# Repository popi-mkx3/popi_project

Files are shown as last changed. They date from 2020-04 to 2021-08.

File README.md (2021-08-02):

# POPI


<br>
<br>

## News : Walko
Below are the links to the follow up of the POPI project, on a new quadruped. Our whole work will be once again open source and we should start releasing it in September 2021. <br>
The goal is still the same : allowing everybody to build their own quad. Unlike POPI, our new quad will be 100% 3d-printed to make this goal closer, with components available to purchase online. We will provide as soon as possible a BOM and links to the manufacturers' websites (we are not resellers). <br>
According to our current estimations, building your own quad will cost around 2,7k€ altogether (without the camera module though), which is still expensive but rather cheap when considering the size of the robot and the price of similar-sized robots.
<br>
We aim to provide beginner-friendly step-by-step instructions along the road, and to keep improving the tech as well.
<br>
<br>
If you want to stay tuned about this : <br>
[Website](https://walko-robotics.com) <br>
[GitLab](https://gitlab.com/walko-robotics/doge/software) and [GitHub](https://github.com/Walko-Robotics) - Please keep in mind that the GitHub repo will be a mirror of the GitLab one from now on. <br>
[Instagram](https://www.instagram.com/walko_adventures/) <br>
[Discord](dsc.gg/walko) <br>
[YouTube](https://www.youtube.com/c/WalkoRobotics) <br> <br>
Fair warning : we mainly use French on our social media for now, but you can still DM us or send us an email at contact.walko@gmail.com if you want.
<br> <br>

## Overview of the project
POPI is an entirely open-source quadruped robot. Though not yet extremely agile, <a href="#team">we</a> meant it to be accessible to anyone interested in robotics and we hope it becomes a friendly collaborative platform for educational or research purposes. You will hence find in this repository everything there is to know about POPI. If you want to know about every details, a good way would be to have a look at the user manual in the [popi_reports] folder.

This project initially started as a student work. As a team of 10 not-yet engineers, we designed and built it from scratch with a 4k€ budget over a six-month-long period during which we still had to take other classes and exams. As such, we are proud of what we achieved but we do know POPI couldn't compete with other quadrupeds as-is. Some of us are still working on this prototype on our free time to improve it, and we will share here everything. In the same time we are also rethinking the whole design to create a new, lighter and mostly 3D-printed POPI.

We are actually looking for some fundings to get this new version up and running and are interested in any opportunity we could have to continue our work. If you have any idea about this or would like to discuss some kind of partnership, please let us know by sending us an <a href = "mailto: popi.mkx3@gmail.com">email</a>.

Otherwise, you can still have a look at what we've done so far on this first prototype. Please keep in mind we inevitably made some mistakes considering it is our first robot and we had limited time and budget. We'll be more than happy to get some advice and discuss any part of our work with you.

#### What is available
:heavy_check_mark: User manual  
:heavy_check_mark: Bill of materials  
:heavy_check_mark: Mechanical drawings and CAD files  
:heavy_check_mark: Electrical drawings  
:heavy_check_mark: Source code (ROS and C++)  
:heavy_check_mark: Cool 3D-renders and wallpapers  
<br>
<br>

<p align="center">
  <a href="#build">Build your own POPI</a> •
  <a href="#contribute">Contribute</a> •
  <a href="#alternative">Other open-source quadrupeds</a> •
  <a href="#team">Meet the team</a> •
  <a href="#acknowledgments">Acknowledgments</a>
</p>

<p align="center">
<a target="_blank" rel="noopener noreferrer" href="https://www.youtube.com/watch?v=yvZBiybOPDk" title="Watch the teaser on YouTube">Watch the teaser on YouTube</a>
</p>

##  Build your own POPI
We really hope you build your own POPI, and if that's the case and you ever need our help, we'll be happy to answer all your questions. To get you going you will find all the CAD files and mechanical drawings in the [popi_mechanics] folder, along with information about POPI's dimensions, its actuators' specifications and the machines we used to make its parts.

In [popi_electronics] you will learn more about POPI's electrical needs, its wiring maps and the electronic supplies. You can also check the whole bill of materials [here](https://github.com/popi-mkx3/popi_project/blob/master/popi_reports/POPI_bill_of_materials.xlsx).

The source code is entirely based on [ROS]. <b>Even if you don't plan on building POPI, you can still develop your own code or your own walking trajectories and try it on a virtual POPI !</b> The instructions to download the source code and use it are available in the [popi_software] folder. Of course you will also find there more explanations about how it works to help you getting started.
<br>
<br>

## Contribute
In times when [ICRA] organizes workshops called *["Towards real-world deployment of legged robots"](https://www.youtube.com/watch?v=nKZdYw9eXY0)*, and when big shots like MIT and Boston Dynamics [loan](http://news.mit.edu/2019/mit-mini-cheetah-first-four-legged-robot-to-backflip-0304) or [sell](https://spectrum.ieee.org/automaton/robotics/industrial-robots/boston-dynamics-spot-robot-dog-goes-on-sale) their robots, we hope our modest open-source alternative can contribute to spread this technology.

The whole point of making this project fully open-source is to have anyone who is interested contribute to POPI ! Whether it includes documentation translations, new functionalities, bug fixes or code improvements, we'll be glad to receive your pull request.

We're fully aware we still have a long road to go before POPI becomes a more autonomous robot, and we'll be happy to take anyone with us onboard. You can see here the list of [contributors](https://github.com/popi-mkx3/popi_project/graphs/contributors) who participated in this project.
<br>
<br>

##  Other open-source quadrupeds
Other open-source quadruped robots already exist ! If you are interested, you can check out the [Stanford Doggo Project] or the [Open Dynamic Robot Initiative] which are really cool and more functional at this point in time.

If you know of other advanced open-source robots do not hesitate to contact us, we will be really happy to have a look at other projects.
<br>
<br>

##  Meet the team !
POPI was initially designed as part of our mechatronical engineering degree at IMT Mines d'Alès in France. Here is the team who started this project.
If you want to contact us you can send us an email at popi.mkx3@gmail.com.

<br>
<p align="center"><b> Project Leader </b></p>
<p align="center">
  <a target="_blank" rel="noopener noreferrer" href="https://www.linkedin.com/in/clément-thomaso-6b9ab910b/">Clément Thomaso</a>
</p>

<p align="center"><b> Mechanics </b> &nbsp; &nbsp; &nbsp; &nbsp; &nbsp; &nbsp; &nbsp; &nbsp; &nbsp; &nbsp; &nbsp; &nbsp; &nbsp; &nbsp; &nbsp; &nbsp; &nbsp; &nbsp; &nbsp; &nbsp; &nbsp; &nbsp; &nbsp; <b> Electronics </b> &nbsp; &nbsp; &nbsp; &nbsp; &nbsp; &nbsp; &nbsp; &nbsp; &nbsp; &nbsp; &nbsp; &nbsp; &nbsp; &nbsp; &nbsp; &nbsp; &nbsp; &nbsp; &nbsp; &nbsp; &nbsp; &nbsp; &nbsp; <b> Programming </b></p>

<p align="center">
  <a target="_blank" rel="noopener noreferrer" href="https://www.linkedin.com/in/rémi-combacal-16032214a/">Rémi Combacal</a>
  <a target="_blank" rel="noopener noreferrer" href="https://www.linkedin.com/in/anaïs-gutton-655383a6/">Anaïs Aharram-Gutton</a>
  <a target="_blank" rel="noopener noreferrer" href="https://www.linkedin.com/in/olivier-peres/">Olivier Peres</a>
  <a target="_blank" rel="noopener noreferrer" href="https://www.linkedin.com/in/guillaume-rougé-913a10108/">Guillaume Rougé</a>
  <a target="_blank" rel="noopener noreferrer" href="https://www.linkedin.com/in/clémence-graton-a02200174/">Clémence Graton</a>
  <a target="_blank" rel="noopener noreferrer" href="https://www.linkedin.com/in/jean-pelloux-prayer-b38a32143/">Jean Pelloux-Prayer</a>
  <a target="_blank" rel="noopener noreferrer" href="https://www.linkedin.com/in/yannis-oddon-442717128/">Yannis Oddon</a>
  <a target="_blank" rel="noopener noreferrer" href="https://www.linkedin.com/in/karla-brottet-69440/">Karla Brottet</a>
  <a target="_blank" rel="noopener noreferrer" href="https://www.linkedin.com/in/lucas-labarussiat/">Lucas Labarussiat</a>
</p>
<br>
<br>

## Acknowledgments
First we would like to thank deeply [Alexander W. Winkler] and [Dave Coleman] for their respective work on [Towr] and [ROS control boilerplate].  
Then let us thank [TiMOTION] who gave us some precious advice along with our knee actuators. Without their contribution, POPI wouldn't be able to lift his legs !  
Finally we of course want to express our sincere gratitude to all our teachers from [IMT Mines d'Alès] who gave us the opportunity to undertake this project and were there to lend us a hand when we needed it the most.
<br>
<br>

 &nbsp; &nbsp; &nbsp; &nbsp; &nbsp; &nbsp; &nbsp; &nbsp; &nbsp; &nbsp; &nbsp; &nbsp; &nbsp;  &nbsp; &nbsp; &nbsp; &nbsp; &nbsp; &nbsp; &nbsp; &nbsp; &nbsp; &nbsp; &nbsp; &nbsp; &nbsp; 

[popi_reports]: https://github.com/popi-mkx3/popi_project/tree/master/popi_reports
[popi_mechanics]: https://github.com/popi-mkx3/popi_project/tree/master/popi_mechanics
[popi_electronics]: https://github.com/popi-mkx3/popi_project/tree/master/popi_electronics
[popi_software]: https://github.com/popi-mkx3/popi_project/tree/master/popi_software

[ROS]: https://www.ros.org/
[Towr]: https://github.com/ethz-adrl/towr
[rqt_bag]: http://wiki.ros.org/rqt_bag
[xpp]: http://wiki.ros.org/xpp
[RViz]: http://wiki.ros.org/rviz
[URDF]: http://wiki.ros.org/urdf
[Gazebo]: http://gazebosim.org/
[rqt_gui]: http://wiki.ros.org/rqt_gui
[ROS Melodic]: http://wiki.ros.org/melodic/Installation/Ubuntu

[BalenaEtcher]: https://www.minimachines.net/tutos/etcher-flasher-image-usb-50144
[ROS control boilerplate]: https://github.com/PickNikRobotics/ros_control_boilerplate

[Alexander W. Winkler]: https://www.alex-winkler.com
[Dave Coleman]: http://dav.ee/
[TiMOTION]: https://www.timotion.com/fr
[IMT Mines d'Alès]: https://www.mines-ales.fr/
[ICRA]: https://www.icra2020.org/
[Stanford Doggo Project]: https://github.com/Nate711/StanfordDoggoProject/blob/master/README.md
[Open Dynamic Robot Initiative]: https://open-dynamic-robot-initiative.github.io/
[YouTube channel]: https://www.youtube.com/channel/UCaCy-1MX6SoqdtjZH4uU_TA

[Clément]: https://www.linkedin.com/in/clément-thomaso-6b9ab910b/
[Rémi]: https://www.linkedin.com/in/rémi-combacal-16032214a/
[Anaïs]: https://www.linkedin.com/in/anaïs-gutton-655383a6/
[Olivier]: https://www.linkedin.com/in/olivier-peres/
[Guillaume]: https://www.linkedin.com/in/guillaume-rougé-913a10108/
[Clémence]: https://www.linkedin.com/in/clémence-graton-a02200174/
[Jean]: https://www.linkedin.com/in/jean-pelloux-prayer-b38a32143/
[Yannis]: https://www.linkedin.com/in/yannis-oddon-442717128/
[Karla]: https://www.linkedin.com/in/karla-brottet-69440/
[Lucas]: https://www.linkedin.com/in/lucas-labarussiat/

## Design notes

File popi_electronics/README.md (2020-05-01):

# popi_electronics


<br>
<br>

You will find here everything you need to understand all the electronics necessary to make POPI walk. Hence, all the [wiring diagrams] and the [pin planning] of our onboard-computers are available in this folder. These files unfortunately are in French for now, but the diagrams should still speak to anyone. Let us know if you ever need a translation and we'll do our best ! To get an overview of POPI's electronic design, please read the following information.

#### What is available
:heavy_check_mark: Design made with [easyEDA]  
:heavy_check_mark: Creation of a custom [encoder]  
:heavy_check_mark: Creation of a custom [current sensor PCB]  
:heavy_check_mark: Mapping of all the card to respect the symmetry  
:heavy_check_mark: PCB manufacturing on a PCB milling machine
<br>
<br>

<p align="center">
  <a href="#general-description">General description</a> •
  <a href="#onboard-computers">Onboard computers</a> •
  <a href="#sensors">Sensors</a> •
  <a href="#power-supply">Power supply</a> •
  <a href="#lets-look-further">Let's look further</a> •
  <a href="#contribute">Contribute</a> •
  <a href="#team">Meet the team</a>
</p>

<p align="center">
	
</p>

##  General description
Most of the electronics of the robot is located on the main electronic board underneath the plexiglass carter. All the parts are spread and layered evenly to ease the accessibility and the maintenance. As you can see below, the main electronic board is divided in 3 areas : computing, commanding and supplying.  
<p align="center">
	
</p>

All the details of the parts is given in the [electronic nomenclature] and a link to a retailer can be found in the [bills of material] in the [popi_report] repository. 
<br>
<br>

##  Onboard computers
POPI is embedded with 3 onboard computers. The main one is a [Raspberry Pi 3B+] and is used to host the controllers and compute the set point of each joint. It communicates with two [BeagleBone Black] (BBB) computers, each one managing the sensors and actuators of two legs (right legs for one BBB and left legs for the other). 

<p align="center">
	 
</p>
<br>
<br>

##  Sensors
In order to know the position of each joint, POPI is embedded with two kind of sensors. The knee and hip rolling joints positions are measured by potentiometers. For the hip pitching joints, we designed a custom [encoder] and its control PCB whose plan is available in this folder. 
<p align="center">
	 
</p>

We also designed a [current sensor PCB] to be able to know the consumption of the motors. All the details of this part are given in here.  
<br>
<br>
 
##  Power supply
POPI is actually powered by two 24V power supplies that are located outside the robot on a [power supply board] we designed. Thus, POPI must be hooked up with an umbilicus cable that will provide the power. Details about this power supply board are given in the [user manual]. 
<p align="center">
	 
</p>

##  Let's look further
This design remains a proof of concept, designed and built in a few months by students relatively new to this field. We now have to improve what we've done and take into account the problems we encountered to achieve a truly functional V2.
  
#### Thoughts for a future version:
* Try looking for more power efficient motors to reduce the size of the ombilicus cable and even maybe to design an onboard battery. 
* Be more careful of ECM influence on the quality of the sensor signals. Try having all the high power beneath the main electronic board and isolate better the two zones. Think about shielding the important data cables. 
* Try having always absolute sensors or at least add limit switches to the system. 
* Unfortunately we had not enough analog input to receive all the current sensor data in the same time. Try adding a multiplexer or an ADC on the current sensor PCB. 
* We had to add 100nF capacitors just before the BeagleBone to filter the analog signal of our potentiometers. Try designing a proper integration board for those capacitors.
<br>
<br>

## Contribute
The whole point of making this project fully open-source is to have anyone who is interested contribute to POPI ! Whether it includes documentation translations, new functionalities, bug fixes or code improvements, we'll be glad to receive your pull request.

We're fully aware we still have a long road to go before POPI becomes a more autonomous robot, and we'll be happy to take anyone with us onboard. You can see here the list of [contributors](https://github.com/popi-mkx3/popi_project/graphs/contributors) who participated in this project.
<br>
<br>

##  Meet the team !
If you want to contact us you can send us an email at popi.mkx3@gmail.com.

<p align="center"><b> Project Leader </b></p>
<p align="center">
  <a target="_blank" rel="noopener noreferrer" href="https://www.linkedin.com/in/clément-thomaso-6b9ab910b/">Clément Thomaso</a>
</p>

<p align="center"><b> Mechanics </b> &nbsp; &nbsp; &nbsp; &nbsp; &nbsp; &nbsp; &nbsp; &nbsp; &nbsp; &nbsp; &nbsp; &nbsp; &nbsp; &nbsp; &nbsp; &nbsp; &nbsp; &nbsp; &nbsp; &nbsp; &nbsp; &nbsp; &nbsp; <b> Electronics </b> &nbsp; &nbsp; &nbsp; &nbsp; &nbsp; &nbsp; &nbsp; &nbsp; &nbsp; &nbsp; &nbsp; &nbsp; &nbsp; &nbsp; &nbsp; &nbsp; &nbsp; &nbsp; &nbsp; &nbsp; &nbsp; &nbsp; &nbsp; <b> Programming </b></p>

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

 &nbsp; &nbsp; &nbsp; &nbsp; &nbsp; &nbsp; &nbsp; &nbsp; &nbsp; &nbsp; &nbsp; &nbsp; &nbsp;  &nbsp; &nbsp; &nbsp; &nbsp; &nbsp; &nbsp; &nbsp; &nbsp; &nbsp; &nbsp; &nbsp; &nbsp; &nbsp; 

[wiring diagrams]: https://github.com/popi-mkx3/popi_project/blob/master/popi_electronics/POPI_PlanElec_General.pdf
[pin planning]: https://github.com/popi-mkx3/popi_project/blob/master/popi_electronics/POPI_PinPlanning.xlsx
[easyEDA]: https://easyeda.com/fr
[encoder]:https://github.com/popi-mkx3/popi_project/blob/master/popi_electronics/POPI_PlanElec_Carte_roue_codeuse.pdf
[current sensor PCB]: https://github.com/popi-mkx3/popi_project/blob/master/popi_electronics/POPI_PlanElec_Capteur_courant.pdf
[electronic nomenclature]: https://github.com/popi-mkx3/popi_project/blob/master/popi_electronics/Nomenclature.xlsx
[bills of material]: https://github.com/popi-mkx3/popi_project/blob/master/popi_reports/POPI_bill_of_materials.xlsx
[Raspberry Pi 3B+]: https://www.raspberrypi.org/products/raspberry-pi-3-model-b-plus/
[BeagleBone Black]: https://beagleboard.org/black
[power supply board]: https://github.com/popi-mkx3/popi_project/blob/master/popi_electronics/Schematic_POPI-Platine-dalimentation_Sheet_1.pdf
[user manual]: https://github.com/popi-mkx3/popi_project/blob/master/popi_reports/POPI_user_manual.pdf
[popi_reports]: https://github.com/popi-mkx3/popi_project/tree/master/popi_reports

[Clément]: https://www.linkedin.com/in/clément-thomaso-6b9ab910b/
[Rémi]: https://www.linkedin.com/in/rémi-combacal-16032214a/
[Anaïs]: https://www.linkedin.com/in/anaïs-gutton-655383a6/
[Olivier]: https://www.linkedin.com/in/olivier-peres/
[Guillaume]: https://www.linkedin.com/in/guillaume-rougé-913a10108/
[Clémence]: https://www.linkedin.com/in/clémence-graton-a02200174/
[Jean]: https://www.linkedin.com/in/jean-pelloux-prayer-b38a32143/
[Yannis]: https://www.linkedin.com/in/yannis-oddon-442717128/
[Karla]: https://www.linkedin.com/in/karla-brottet-69440/
[Lucas]: https://www.linkedin.com/in/lucas-labarussiat/

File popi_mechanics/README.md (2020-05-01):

# popi_mechanics


<br>
<br>

You will find here everything you need for the [machining] and the [assembly] as well as the [mechanical drawings] of this 71kg and 1 meter long robot. These files unfortunately are in French for now, but the drawings should still speak to anyone. Let us know if you ever need a translation and we'll do our best ! To get an overview of POPI's mechanical design, please read the following information.

#### What is available
:heavy_check_mark: Design made with [CATIA]  
:heavy_check_mark: First estimates of forces and torques on [SimDesigner]  
:heavy_check_mark: Mechanical simulation and actuator's choice on [SolidWorks] Motion and [SolidWorks] Simulation  
:heavy_check_mark: Machining with CNC milling and turning machines, water jet cutting and 3D printing  
:heavy_check_mark: Rendering with [SolidWorks] Motion and [SolidWorks] PhotoView 360  
<br>
<br>

<p align="center">
  <a href="#general-description">General description</a> •
  <a href="#how-it-works">How it works</a> •
  <a href="#lets-look-further">Let's look further</a> •
  <a href="#contribute">Contribute</a> •
  <a href="#team">Meet the team</a>
</p>

<p align="center">
<a target="_blank" rel="noopener noreferrer" href="https://www.youtube.com/watch?v=yvZBiybOPDk" title="Watch the teaser on YouTube">Watch the teaser on YouTube</a>
</p>

##  General description
When standing in its nominal position, POPI has the following general dimensions: 1017mm x 662mm x 620mm (DxLxH). The general assembly is available in the [CATIA folder]. You can download the whole folder and open the top assembly "ALL10-FinalVersion.CATProduct" with CATIA V5.
<p align="center">
	
</p>

As shown below, some accessories are needed for the proper handling of the robot, such as a base and handles. Their CAD is available as well in the [CATIA folder] with the respective names ["Socle"] and ["Poignee"].

<p align="center">
	 
</p>
<br>
<br>

##  How it works
POPI has a longitudinal axis of symmetry.

<p align="center">
	 
</p>
<br>
<br>
POPI is composed of 12 actuators, 3 per leg. The combination of the "pitching hip joint" and "knee joint" actuators allows the robot to operate linearly. The action of the "rolling hip joint" allows the robot to turn and keep balance. You can find details about the actuators [here].

<p align="center">
	 
</p>
<br>
<br>
Zoom on a leg and its actuators without the body:
<p align="center">
	 
</p>
<br>
<br>

##  Let's look further
This design remains a proof of concept, designed and built in a few months by students relatively new to this field. We now have to improve what we've done and take into account the problems we encountered to achieve a truly functional V2.
  
#### Thoughts for a future version:
* Do not make legs too heavy compared to the body and think ahead about the robot's balance. We currently have too much weight on the back compared to the front, so the rear feet are struggling to get off the ground.
* Think about the programming in parallel of mechanics, try out all possible approaches in a physical simulation of walking before machining the robot. SolidWorks Motion does this perfectly. 
* Our robot can move all of its joints independently, it's cool, but think about whether this is really useful. Moving the robot's pitch hip proportionally to the knee might be enough.
* Our robot is built in a simple way, that's the goal, but a slightly more complex arrangement that would allow the knee to move without a cylinder could be more efficient. A motor, which could be integrated into the body and act on the knee through a chain/pulley system might be a better solution.
<br>
<br>

## Contribute
The whole point of making this project fully open-source is to have anyone who is interested contribute to POPI ! Whether it includes documentation translations, new functionalities, bug fixes or code improvements, we'll be glad to receive your pull request.

We're fully aware we still have a long road to go before POPI becomes a more autonomous robot, and we'll be happy to take anyone with us onboard. You can see here the list of [contributors](https://github.com/popi-mkx3/popi_project/graphs/contributors) who participated in this project.
<br>
<br>

##  Meet the team !
If you want to contact us you can send us an email at popi.mkx3@gmail.com.

<p align="center"><b> Project Leader </b></p>
<p align="center">
  <a target="_blank" rel="noopener noreferrer" href="https://www.linkedin.com/in/clément-thomaso-6b9ab910b/">Clément Thomaso</a>
</p>

<p align="center"><b> Mechanics </b> &nbsp; &nbsp; &nbsp; &nbsp; &nbsp; &nbsp; &nbsp; &nbsp; &nbsp; &nbsp; &nbsp; &nbsp; &nbsp; &nbsp; &nbsp; &nbsp; &nbsp; &nbsp; &nbsp; &nbsp; &nbsp; &nbsp; &nbsp; <b> Electronics </b> &nbsp; &nbsp; &nbsp; &nbsp; &nbsp; &nbsp; &nbsp; &nbsp; &nbsp; &nbsp; &nbsp; &nbsp; &nbsp; &nbsp; &nbsp; &nbsp; &nbsp; &nbsp; &nbsp; &nbsp; &nbsp; &nbsp; &nbsp; <b> Programming </b></p>

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

 &nbsp; &nbsp; &nbsp; &nbsp; &nbsp; &nbsp; &nbsp; &nbsp; &nbsp; &nbsp; &nbsp; &nbsp; &nbsp;  &nbsp; &nbsp; &nbsp; &nbsp; &nbsp; &nbsp; &nbsp; &nbsp; &nbsp; &nbsp; &nbsp; &nbsp; &nbsp; 

[mechanical drawings]: https://github.com/popi-mkx3/popi_project/tree/master/popi_mechanics/mechanical_drawings
[machining]: https://github.com/popi-mkx3/popi_project/blob/master/popi_mechanics/mechanical_drawings/POPI_PlanMeca_Usinage.pdf
[assembly]: https://github.com/popi-mkx3/popi_project/blob/master/popi_mechanics/mechanical_drawings/POPI_PlanMeca_Notice_de_montage.pdf
[CATIA]: https://i.imgur.com/riZaPoB.png
[SimDesigner]: https://i.imgur.com/Nx55Sqr.png
[SolidWorks]: https://i.imgur.com/M5bYSk7.png

[CATIA folder]: https://github.com/popi-mkx3/popi_project/tree/master/popi_mechanics/CATIA
["Socle"]: https://github.com/popi-mkx3/popi_project/blob/master/popi_mechanics/CATIA/Socle.CATPart
["Poignee"]: https://github.com/popi-mkx3/popi_project/blob/master/popi_mechanics/CATIA/Poignee.CATPart

[here]: https://github.com/popi-mkx3/popi_project/blob/master/popi_mechanics/POPI_actuators_data.xlsx

[popi_reports]: https://github.com/popi-mkx3/popi_reports
[ROS]: https://www.ros.org/
[Towr]: https://github.com/ethz-adrl/towr
[rqt_bag]: http://wiki.ros.org/rqt_bag
[xpp]: http://wiki.ros.org/xpp
[RViz]: http://wiki.ros.org/rviz
[URDF]: http://wiki.ros.org/urdf
[Gazebo]: http://gazebosim.org/
[rqt_gui]: http://wiki.ros.org/rqt_gui
[ROS Melodic]: http://wiki.ros.org/melodic/Installation/Ubuntu

[BalenaEtcher]: https://www.minimachines.net/tutos/etcher-flasher-image-usb-50144
[ROS control boilerplate]: https://github.com/PickNikRobotics/ros_control_boilerplate

[Alexander W. Winkler]: https://www.alex-winkler.com
[Dave Coleman]: http://dav.ee/
[TiMOTION]: https://www.timotion.com/fr
[IMT Mines d'Alès]: https://www.mines-ales.fr/

[Clément]: https://www.linkedin.com/in/clément-thomaso-6b9ab910b/
[Rémi]: https://www.linkedin.com/in/rémi-combacal-16032214a/
[Anaïs]: https://www.linkedin.com/in/anaïs-gutton-655383a6/
[Olivier]: https://www.linkedin.com/in/olivier-peres/
[Guillaume]: https://www.linkedin.com/in/guillaume-rougé-913a10108/
[Clémence]: https://www.linkedin.com/in/clémence-graton-a02200174/
[Jean]: https://www.linkedin.com/in/jean-pelloux-prayer-b38a32143/
[Yannis]: https://www.linkedin.com/in/yannis-oddon-442717128/
[Karla]: https://www.linkedin.com/in/karla-brottet-69440/
[Lucas]: https://www.linkedin.com/in/lucas-labarussiat/

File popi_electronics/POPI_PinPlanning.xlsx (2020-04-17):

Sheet: BeagleBoneBlack_Gauche
P8 |  |  |  | P9
 | 46 |  | 45 |  | 46 |  | 45
 | 44 |  | 43 |  | 44 |  | 43
 | 42 |  | 41 |  | 42 |  | 41
 | 40 |  | 39 | ANA-Aile-Potar-AVG | 40 | ANA-Aile-Potar-ARG | 39
 | 38 |  | 37 | ANA-Coude-Potar-AVG | 38 | ANA-Coude-Potar-ARG | 37
 | 36 |  | 35 | ANA-Aile-Cour-ARG | 36 | ANA-Epaule-Cour-ARG | 35
 | 34 |  | 33 |  | 34 | ANA-Coude-Cour-ARG | 33
 | 32 |  | 31 | 1,8V | 32 | SPI-SCK-QECG | 31
 | 30 |  | 29 | SPI-MOSI-QECG | 30 | SPI-MISO-QECG | 29
 | 28 |  | 27 | SPI-CS2-QECG | 28 | SPI-CS1-QECG | 27
TOR-Courant-1-AVG | 26 |  | 25 |  | 26 |  | 25
 | 24 |  | 23 |  | 24 |  | 23
 | 22 |  | 21 | PWM-Aile-AVG | 22 | PWM-Aile-ARG | 21
 | 20 | PWM-Coude-ARG | 19 |  | 20 |  | 19
TOR-Courant-1-ARG | 18 | TOR-Courant-2-AVG | 17 |  | 18 |  | 17
TOR-Courant-2-ARG | 16 | TOR-Courant-3-AVG | 15 | PWM-Epaule-ARG | 16 |  | 15
TOR-Courant-3-ARG | 14 | PWM-Coude-AVG | 13 | PWM-Epaule-AVG | 14 |  | 13
DIR-Coude-ARG | 12 | DIR-Aile-ARG | 11 |  | 12 |  | 11
DIR-Epaule-ARG | 10 | DIR-Coude-AVG | 9 |  | 10 |  | 9
DIR-Aile-AVG | 8 | DIR-Epaule-AVG | 7 |  | 8 |  | 7
 | 6 |  | 5 |  | 6 | 5V | 5
 | 4 |  | 3 |  | 4 |  | 3
 | 2 |  | 1 |  | 2 | GND | 1
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

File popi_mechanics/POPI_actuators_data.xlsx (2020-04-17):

Epaule |  |  | Lien vers le site
Ref Moteur | MY1016 | unité | http://pocketquadelectrique.csmoto.fr/informations/datasheet2.php
Vitesse nominale | 2750 | rpm
Couple à 2750 tr/min | 1.22 | N.m
Courant à 2750 tr/min chargé | 18.7 | A
Poids | 2.53 | kg
Ref Réducteur | PLFE-090-100-SSSE3AE-R10 | unité | https://www.neugart.com/fr-fr/sav/outils-et-formations/tec-data-finder/
Réduction | 100 | -
Nombre d'étage | 2 | -
Rendement à pleine charge | 97 | %
Poids | 3.09 | kg
Aile |  |  | Lien vers le site
Ref Motoréducteur | MR977 63 1/96 | unité | http://www.bernio.it/en/mr-977-64.html
Vitesse nominale | 30 | rpm
Vitesse pour I=7.5A | 22 | rpm
Couple pour I=7.5A | 43 | N.m
Couple max | 120 | N.m
Poids | 3.4 | kg
Coude |  |  | Lien vers le site
Ref Vérin | MA2-2G-150334-36 110-122-600 | unité | https://www.timotion.com/fr/product/detail/linear-actuators/ma2-series?upcls=1481269298&guid=1488425822
Max push/pull load | 2000 | N
Courant non chargé | 2.4 | A
Courant à charge max | 7.5 | A
Vitesse non chargé | 25.5 | mm/s
Vitesse à charge max | 22.3 | mm/s
Potentiomètre | 10 | kOhm
Potentiomètre vérin rétracté | 0.6 | kOhm
Potentiomètre vérin étendu | 5.3 | kOhm
Course | 150 | mm
Poids | 3.1 | kg
Classe IP | IP66 | -

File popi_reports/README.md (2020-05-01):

# popi_reports


<br>
<br>

You will find here the bill of materials and the user manual which offers a complete documentation of our project. This manual unfortunately is in French for now, but the README files included in the different folders of this repository should already give you a clear understanding of the project. Let us know if you ever need a translation and we'll do our best !
<br>
<br>

## Contribute
The whole point of making this project fully open-source is to have anyone who is interested contribute to POPI ! Whether it includes documentation translations, new functionalities, bug fixes or code improvements, we'll be glad to receive your pull request.

We're fully aware we still have a long road to go before POPI becomes a more autonomous robot, and we'll be happy to take anyone with us onboard. You can see here the list of [contributors](https://github.com/popi-mkx3/popi_project/graphs/contributors) who participated in this project.
<br>
<br>

## Meet the team !
If you want to contact us you can send us an email at popi.mkx3@gmail.com.

<p align="center"><b> Project Leader </b></p>
<p align="center">
  <a target="_blank" rel="noopener noreferrer" href="https://www.linkedin.com/in/clément-thomaso-6b9ab910b/">Clément Thomaso</a>
</p>

<p align="center"><b> Mechanics </b> &nbsp; &nbsp; &nbsp; &nbsp; &nbsp; &nbsp; &nbsp; &nbsp; &nbsp; &nbsp; &nbsp; &nbsp; &nbsp; &nbsp; &nbsp; &nbsp; &nbsp; &nbsp; &nbsp; &nbsp; &nbsp; &nbsp; &nbsp; <b> Electronics </b> &nbsp; &nbsp; &nbsp; &nbsp; &nbsp; &nbsp; &nbsp; &nbsp; &nbsp; &nbsp; &nbsp; &nbsp; &nbsp; &nbsp; &nbsp; &nbsp; &nbsp; &nbsp; &nbsp; &nbsp; &nbsp; &nbsp; &nbsp; <b> Programming </b></p>

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

 &nbsp; &nbsp; &nbsp; &nbsp; &nbsp; &nbsp; &nbsp; &nbsp; &nbsp; &nbsp; &nbsp; &nbsp; &nbsp;  &nbsp; &nbsp; &nbsp; &nbsp; &nbsp; &nbsp; &nbsp; &nbsp; &nbsp; &nbsp; &nbsp; &nbsp; &nbsp; 

[wiring diagrams]: https://github.com/popi-mkx3/popi_project/blob/master/popi_electronics/POPI_PlanElec_General.pdf
[pin planning]: https://github.com/popi-mkx3/popi_project/blob/master/popi_electronics/POPI_PinPlanning.xlsx
[easyEDA]: https://easyeda.com/fr
[encoder]:https://github.com/popi-mkx3/popi_project/blob/master/popi_electronics/POPI_PlanElec_Carte_roue_codeuse.pdf
[current sensor PCB]: https://github.com/popi-mkx3/popi_project/blob/master/popi_electronics/POPI_PlanElec_Capteur_courant.pdf
[electronic nomenclature]: https://github.com/popi-mkx3/popi_project/blob/master/popi_electronics/Nomenclature.xlsx
[bills of material]: https://github.com/popi-mkx3/popi_project/blob/master/popi_reports/POPI_bill_of_materials.xlsx
[Raspberry Pi 3B+]: https://www.raspberrypi.org/products/raspberry-pi-3-model-b-plus/
[BeagleBone Black]: https://beagleboard.org/black
[power supply board]: https://github.com/popi-mkx3/popi_project/blob/master/popi_electronics/Schematic_POPI-Platine-dalimentation_Sheet_1.pdf
[user_manual]: https://github.com/popi-mkx3/popi_project/blob/master/popi_reports/POPI_user_manual.pdf

[Clément]: https://www.linkedin.com/in/clément-thomaso-6b9ab910b/
[Rémi]: https://www.linkedin.com/in/rémi-combacal-16032214a/
[Anaïs]: https://www.linkedin.com/in/anaïs-gutton-655383a6/
[Olivier]: https://www.linkedin.com/in/olivier-peres/
[Guillaume]: https://www.linkedin.com/in/guillaume-rougé-913a10108/
[Clémence]: https://www.linkedin.com/in/clémence-graton-a02200174/
[Jean]: https://www.linkedin.com/in/jean-pelloux-prayer-b38a32143/
[Yannis]: https://www.linkedin.com/in/yannis-oddon-442717128/
[Karla]: https://www.linkedin.com/in/karla-brottet-69440/
[Lucas]: https://www.linkedin.com/in/lucas-labarussiat/

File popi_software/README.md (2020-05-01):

# popi_software



*The Gazebo world used here isn't available yet in the repository, as we encountered some problems with it. It comes from this [GitHub project](https://github.com/yukkysaito/vehicle_sim) if you want to check it out.*
<br>
<br>

You will find here all the source code used on POPI. The code is based on [ROS]. You can run it without the robot, develop your own code and try it in a [Gazebo] simulation. Please read below to get all the information needed to install and run our code on a virtual POPI. If you build your own robot and need the instructions to configure the network and make it work, please refer to the user manual in the [popi_reports] folder.

#### What is available
:heavy_check_mark: Trajectory generation and optimization based on [Towr]  
:heavy_check_mark: Easy recording with [rqt_bag]  
:heavy_check_mark: Actuators' control based on [ROS control boilerplate]  
:heavy_check_mark: Available simulation on Gazebo  
<br>
<br>

<p align="center">
  <a href="#soft">POPI software</a> •
  <a href="#install-dependecies">Install dependencies</a> •
  <a href="#structure">Folder structure</a> •
  <a href="#run">Run</a> •
  <a href="#contribute">Contribute</a> •
  <a href="#team">Meet the team</a>
</p>

<p align="center">
	
</p>

##  POPI software
As of now, POPI doesn't have any on-the-fly trajectory computation. Hence it is important to understand there is a two-step operating principle:
   * Generating a new trajectory and making sure it works fine on the virtual model
   * Sending the trajectory on POPI

The brains of POPI are split between 3 single-board computers (one Raspberry Pi 3B+ and two BeagleBone Black) and one (offboard) user computer. It can seem daunting at first, but it allows for a more distributed work, and endows POPI with a computational power that is sufficient even for its future developments. Moreover the source code is entirely based on [ROS], which makes it really easy to run code across multiple machines.

Each computer has a special use, as shown on the diagram below.
<p align="center">
   
</p>

If you build your own POPI, you will need to download the [flash images] for the 3 SD cards. The source code available here is actually the one running on the user computer when making POPI walk, and it is also the one needed to create and test new trajectories.
<br>
<br> 

##  Install dependencies
  
The environment we used is Ubuntu 18.04 with [ROS Melodic].
<br>

* First, install [ROS]:
   ```bash
   sudo sh -c 'echo "deb http://packages.ros.org/ros/ubuntu $(lsb_release -sc) main" > /etc/apt/sources.list.d/ros-latest.list'
   sudo apt-key adv --keyserver 'hkp://keyserver.ubuntu.com:80' --recv-key C1CF6E31E6BADE8868B172B4F42ED6FBAB17C654
   sudo apt-get update
   sudo apt-get install ros-melodic-desktop-full
   ```
	Do the following to get the latest version of Gazebo 9 (we used the 9.12.0):
   ```bash
   sudo sh -c 'echo "deb http://packages.osrfoundation.org/gazebo/ubuntu-stable `lsb_release -cs` main" > /etc/apt/sources.list.d/gazebo-stable.list'
   wget http://packages.osrfoundation.org/gazebo.key -O - | sudo apt-key add -
   ```
  
	Then update your packages:
   ```bash
   sudo apt-get update
   sudo apt-get upgrade
   ```
   Finally, install the other dependencies:
   ```bash
   sudo apt-get install ros-melodic-ros-control ros-melodic-ros-controllers ros-melodic-robot-controllers ros-melodic-robot-state-publisher ros-melodic-gazebo-ros-pkgs ros-melodic-gazebo-ros-control ros-melodic-rosparam-shortcuts ros-melodic-joy git cmake libeigen3-dev coinor-libipopt-dev libncurses5-dev libgflags-dev libboost-all-dev xterm
   ```
   If you encounter any problem or would like any details about these dependencies, you will find [here](https://github.com/popi-mkx3/popi_project/blob/master/popi_software/CONFIGURATION.md) a list of the versions of the packages we had installed, as well as links to their respective websites.
<br>

* Create the workspace:
   ```bash
   mkdir -p ~/catkin_ws/src
   cd ~/catkin_ws/src
   ```
* Either download the whole repository:
   ```bash
   git clone https://github.com/popi-mkx3/popi_project.git
   ```
* Or only the popi_software folder:
   ```bash
   git init
   git remode add -f origin https://github.com/popi-mkx3/popi_project.git
   git config core.sparseCheckout true
   echo "popi_software" >> .git/info/sparse-checkout
   git pull origin master
   ```
<br>

* Build the workspace:
   ```bash
   cd ~/catkin_ws
   source /opt/ros/melodic/setup.bash
   catkin_make_isolated
   ```
<br>

* Configuration:  
   Copy the following command to add these four lines to your `~/.bashrc`: 
   ```bash
   echo "source /opt/ros/melodic/setup.bash
   source ~/catkin_ws/devel_isolated/setup.bash
   #export ROS_IP=192.168.7.4
   #export ROS_MASTER_URI=http://192.168.7.1:11311" >> ~/.bashrc

   ```
	Leave the two last lines commented if you're not building your own robot.
<br>
<br>

##  Folder structure
Let's break the folder structure down so that you better understand how it works.
<p align="center">
   
</p>

Here is a short explanation of what lies in each folder:
* [popi_code] includes source code automatically generated from our URDF model with [RobCoGen], using first the [urdf2robcogen] tool to get a .kindsl format. We actually don't use this generated code for now but thought this might be of use at some point.
* [popi_control] is based on [ROS control boilerplate] and includes ROS-type controllers. This is what allows us to control our twelve actuators, in the simulation as well as with the real robot. In the latter case, a hardware interface is needed. It is also included in this package, but the node actually runs on the Raspberry Pi when making POPI walk.
* [popi_description] includes the [URDF] model of POPI and the STL meshes. In fact we first generated the URDF from our mechanical design thanks to the [SolidWorks to URDF exporter], and then made modifications, additions and simplifications to get the current [xacro] model.
* [popi_gazebo] includes the files needed to define the physics of the world where we spawn our virtual POPI. It also includes a [SDF] model of POPI. Although, please note that we created this SDF model early in the project before switching to URDF, which is needed to work with ROS.
* [popi_robot] includes the definition of messages used and the main launch files.
* [ifopt] is a C++ Interface to Nonlinear Programming Solvers used by Towr.
* [towr] is the package used to generate trajectories. It was developed by [Alexander W. Winkler], we only added there our robot model.
* [xpp] is a package used by Towr to allow the visualization of trajectories on RViz. This is where is included the inverse kinematic model of our robot to compute the required joint angles to get the foot in the desired position.
* actionneurs includes ROS nodes sending commands to the actuators (only in the flash images).
* capteurs includes ROS nodes reading the sensors' values (only in the flash images).
<br>
<br>

## Run
* Run Towr to generate a new trajectory:
   ```bash
   roslaunch towr_ros towr_ros_popi.launch
   ```
   The user interface is pretty easy to understand. The constraints used by Towr can make a big difference in the generated trajectories, and to change them you will need to get your hands in the code. The maximum deviation of the feet from the nominal position, represented by the blue boxes, can be changed in *popi_software/towr/towr/towr/include/towr/models/examples/popi_model.h*. We would still have to work with Towr to use the constraints efficiently. Moreover our inverse kinematic model is unfortunately restricted with quite a lot of singularities. To get rid of them, we lowered the maximum deviation parameters, but this probably isn't the best way around.
   We still generated some good trajectories we were able to try out on our real robot and which worked fine !
<br>

* Save the trajectory as a rosbag file:
   ```bash
   cd ~/catkin_ws/src/popi_project/popi_software/popi/popi_robot/trajectories/bags
   rosrun rqt_bag rqt_bag
   ```
   Click the red recording button, select the 12 topics called */popi/.../command*, then click *Record*, give a name to your bag file (like *test.bag*), then go to the towr user interface and click *v* to replay the last calculated trajectory.
   The rqt_bag window should look like this:
   <p align="center">
       
   </p>
   Note the X number, as it may be useful to understand the timestamps of your bag file if you want to work on your commands as a CSV file. When this is done, close the rqt_bag window.
<br>

* To convert your data fril rosbag to CSV, you can do the following:   
   ```bash
   cd ~/catkin_ws/src/popi_project/popi_software/popi/popi_robot/trajectories/bags
   rostopic echo -b test.bag -p /popi/aileAVD_eff_position_controller/command > ../csv/aileAVD.csv
   rostopic echo -b test.bag -p /popi/aileAVG_eff_position_controller/command > ../csv/aileAVG.csv
   rostopic echo -b test.bag -p /popi/aileARD_eff_position_controller/command > ../csv/aileARD.csv
   rostopic echo -b test.bag -p /popi/aileARG_eff_position_controller/command > ../csv/aileARG.csv
   rostopic echo -b test.bag -p /popi/epauleAVD_eff_position_controller/command > ../csv/epauleAVD.csv
   rostopic echo -b test.bag -p /popi/epauleAVG_eff_position_controller/command > ../csv/epauleAVG.csv
   rostopic echo -b test.bag -p /popi/epauleARD_eff_position_controller/command > ../csv/epauleARD.csv
   rostopic echo -b test.bag -p /popi/epauleARG_eff_position_controller/command > ../csv/epauleARG.csv
   rostopic echo -b test.bag -p /popi/coudeAVD_eff_position_controller/command > ../csv/coudeAVD.csv
   rostopic echo -b test.bag -p /popi/coudeAVG_eff_position_controller/command > ../csv/coudeAVG.csv
   rostopic echo -b test.bag -p /popi/coudeARD_eff_position_controller/command > ../csv/coudeARD.csv
   rostopic echo -b test.bag -p /popi/coudeARG_eff_position_controller/command > ../csv/coudeARG.csv
   ```
   This isn't optimal as it creates 12 differents CSV files you then have to concatenate to work on the whole data in one file. We will release a short script to make it easier. To get your timestamps into actual seconds past after your hit the *Record* button, use the following formula : t = (%time / 10^9) − X.
<br>

* If you changed your data on Excel and want to get the modified .csv back into rosbag, make sure first the columns headings are the following : %time, aileAVD, aileAVG, aileARD, aileARG, epauleAVD,
epauleAVG, epauleARD, epauleARG, coudeAVD, coudeAVG, coudeARD, coudeARG. This means the columns need to be in that order, so be careful when you concatenate your 12 CSV files.
You can then save your file, for example as *modified_test.csv*. Make sure the CSV format is the same as the one it was in the previous files. Finally, you can run the following commands:
   ```bash
   cd ~/catkin_ws/src/popi_project/popi_software/popi/popi_robot/trajectories/csv
   ./csv_to_rosbag.py modified_test
   mv modified_test.bag ../bags/
   ```
<br>

* To open the Gazebo environment, you just have to run:
   ```bash
   roslaunch popi_robot popi_simu.launch
   ```
<br>

* If you have a Xbox controller, this launch file allows you to use it to run some simple functions:
<p align="center">
    
</p>

To build your own controls, you can have a look at *popi_software/popi/popi_robot/src/manette.cpp* .
<br>

* Finally, to use the trajectory you just created:
   ```bash
   cd ~/catkin_ws/src/popi_project/popi_software/popi/popi_robot/trajectories/bags
   rosbag play modified_test.bag
   ```
   You can also try out the ones we saved:
   ```bash
   rosbag play short_static_walking.bag
   rosbag play short_dynamic_walking.bag
   rosbag play long_dynamic_walking.bag
   rosbag play pit_30cm.bag
   rosbag play step_20cm.bag
   ```
<br>
<br>

## Contribute
The whole point of making this project fully open-source is to have anyone who is interested contribute to POPI ! Whether it includes documentation translations, new functionalities, bug fixes or code improvements, we'll be glad to receive your pull request.

We're fully aware we still have a long road to go before POPI becomes a more autonomous robot, and we'll be happy to take anyone with us onboard. You can see here the list of [contributors](https://github.com/popi-mkx3/popi_project/graphs/contributors) who participated in this project.
<br>
<br>

##  Meet the team !
If you want to contact us you can send us an email at popi.mkx3@gmail.com.

<p align="center"><b> Project Leader </b></p>
<p align="center">
  <a target="_blank" rel="noopener noreferrer" href="https://www.linkedin.com/in/clément-thomaso-6b9ab910b/">Clément Thomaso</a>
</p>

<p align="center"><b> Mechanics </b> &nbsp; &nbsp; &nbsp; &nbsp; &nbsp; &nbsp; &nbsp; &nbsp; &nbsp; &nbsp; &nbsp; &nbsp; &nbsp; &nbsp; &nbsp; &nbsp; &nbsp; &nbsp; &nbsp; &nbsp; &nbsp; &nbsp; &nbsp; <b> Electronics </b> &nbsp; &nbsp; &nbsp; &nbsp; &nbsp; &nbsp; &nbsp; &nbsp; &nbsp; &nbsp; &nbsp; &nbsp; &nbsp; &nbsp; &nbsp; &nbsp; &nbsp; &nbsp; &nbsp; &nbsp; &nbsp; &nbsp; &nbsp; <b> Programming </b></p>

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

 &nbsp; &nbsp; &nbsp; &nbsp; &nbsp; &nbsp; &nbsp; &nbsp; &nbsp; &nbsp; &nbsp; &nbsp; &nbsp;  &nbsp; &nbsp; &nbsp; &nbsp; &nbsp; &nbsp; &nbsp; &nbsp; &nbsp; &nbsp; &nbsp; &nbsp; &nbsp; 

[popi_reports]: https://github.com/popi-mkx3/popi_project/tree/master/popi_reports
[popi_mechanics]: https://github.com/popi-mkx3/popi_project/tree/master/popi_mechanics
[popi_electronics]: https://github.com/popi-mkx3/popi_project/tree/master/popi_electronics
[popi_software]: https://github.com/popi-mkx3/popi_project/tree/master/popi_software
[popi_code]: https://github.com/popi-mkx3/popi_project/tree/master/popi_software/popi/popi_code
[popi_control]: https://github.com/popi-mkx3/popi_project/tree/master/popi_software/popi/popi_control
[popi_description]: https://github.com/popi-mkx3/popi_project/tree/master/popi_software/popi/popi_description
[popi_gazebo]: https://github.com/popi-mkx3/popi_project/tree/master/popi_software/popi/popi_gazebo
[popi_robot]: https://github.com/popi-mkx3/popi_project/tree/master/popi_software/popi/popi_robot
[towr]: https://github.com/popi-mkx3/popi_project/tree/master/popi_software/towr/towr
[ifopt]: https://github.com/popi-mkx3/popi_project/tree/master/popi_software/towr/ifopt
[xpp]: https://github.com/popi-mkx3/popi_project/tree/master/popi_software/towr/xpp
[flash images]: https://drive.google.com/drive/folders/1-L8BeBzDw7JF44kGpImWbDnX2oDaef4I?usp=sharing

[SolidWorks to URDF exporter]: https://wiki.ros.org/sw_urdf_exporter
[urdf2robcogen]: https://github.com/leggedrobotics/urdf2robcogen
[RobCoGen]: https://robcogenteam.bitbucket.io/whatisit.html
[SDF]: http://sdformat.org/spec
[ROS]: https://www.ros.org/
[Towr]: https://github.com/ethz-adrl/towr
[rqt_bag]: http://wiki.ros.org/rqt_bag
[RViz]: http://wiki.ros.org/rviz
[URDF]: http://wiki.ros.org/urdf
[xacro]: http://wiki.ros.org/xacro
[Gazebo]: http://gazebosim.org/
[rqt_gui]: http://wiki.ros.org/rqt_gui
[ROS Melodic]: http://wiki.ros.org/melodic/Installation/Ubuntu

[BalenaEtcher]: https://www.minimachines.net/tutos/etcher-flasher-image-usb-50144
[ROS control boilerplate]: https://github.com/PickNikRobotics/ros_control_boilerplate

[Alexander W. Winkler]: https://www.alex-winkler.com
[Dave Coleman]: http://dav.ee/
[TiMOTION]: https://www.timotion.com/fr
[IMT Mines d'Alès]: https://www.mines-ales.fr/

[Clément]: https://www.linkedin.com/in/clément-thomaso-6b9ab910b/
[Rémi]: https://www.linkedin.com/in/rémi-combacal-16032214a/
[Anaïs]: https://www.linkedin.com/in/anaïs-gutton-655383a6/
[Olivier]: https://www.linkedin.com/in/olivier-peres/
[Guillaume]: https://www.linkedin.com/in/guillaume-rougé-913a10108/
[Clémence]: https://www.linkedin.com/in/clémence-graton-a02200174/
[Jean]: https://www.linkedin.com/in/jean-pelloux-prayer-b38a32143/
[Yannis]: https://www.linkedin.com/in/yannis-oddon-442717128/
[Karla]: https://www.linkedin.com/in/karla-brottet-69440/
[Lucas]: https://www.linkedin.com/in/lucas-labarussiat/

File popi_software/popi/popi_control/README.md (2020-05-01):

## Credits
<br>
<b>

This is a modified version of the [original repository](https://github.com/PickNikRobotics/ros_control_boilerplate). Please refer to it for an up-to-date version, ROS install commands and pull-requests.
</b>
<br>
<br>
<br>
<br>
<br>
<br>

# ROS Control Boilerplate

Simple simulation interface and template for setting up a hardware interface for ros_control. The idea is you take this as a starting point for creating your hardware interfaces, and it is needed because [ros_control documentation](http://wiki.ros.org/ros_control) is sparse. This boilerplate demonstrates:

 - Creating a hardware_interface for multiple joints for use with ros_control
 - Position Trajectory Controller
 - Control of 2 joints of the simple robot "Popi" pictured below
 - Loading configurations with roslaunch and yaml files
 - Generating a random trajectory and sending it over an actionlib interface
 - Partial support of joint mode switching (needs to be improved)
 - Joint limits
 - Pass-through non-physics based robot simulator
 - Visualization in Rviz

Developed by [Dave Coleman](http://dav.ee/) at the University of Colorado Boulder

<a href='https://ko-fi.com/A7182AMW' target='_blank'>Buy Me a Coffee at ko-fi.com</a>

 *  Travis CI
 * Devel Job Status (http://jenkins.ros.org/job/devel-indigo-popi_control) Devel Job Status
 * Build Status (http://jenkins.ros.org/job/ros-indigo-ros-control-boilerplate_binarydeb_trusty_amd64/) AMD64 Debian Job Status

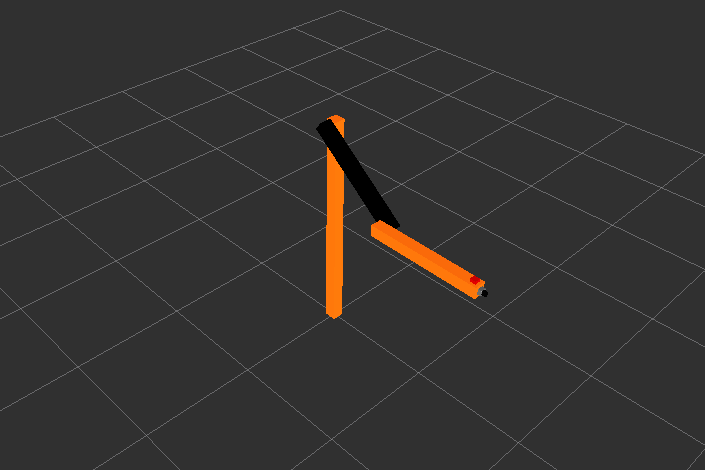
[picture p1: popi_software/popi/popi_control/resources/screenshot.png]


## Video Demo

See [YouTube](https://www.youtube.com/watch?v=Tpj2tx9uZ-o) for a very modest video demo.

## Install

This package depends on [gazebo_ros_demos](https://github.com/ros-simulation/gazebo_ros_demos) for its ``popi_description`` package, but you must add it to your catkin workspace by source:

    git clone https://github.com/ros-simulation/gazebo_ros_demos.git

Then, either install this package from source so you can develop off of it, or install from debian:

    sudo apt-get install ros-indigo-ros-control-boilerplate

## Run Simulation Demo

This package is setup to run the "Popi" two joint revolute-revolute robot demo. This "template package" is located in the popi_control as a subfolder that you can easily rename and reuse. To run its ros_control non-physics-based simulated hardware interface, run:

    roslaunch popi_control popi_simulation.launch

To visualize its published ``/tf`` coordinate transforms in Rviz run:

    roslaunch popi_control popi_visualize.launch

To send a random, dummy trajectory to execute, run:

    roslaunch popi_control popi_test_trajectory.launch

## Customize

To test this as a simulation interface for your robot, you can quickly rename the subfolder package into the name of your robot using the following commands:

```
function findreplace() {
    grep -lr -e "$1" * | xargs sed -i "s/$1/$2/g" ;
}

function findreplacefilename() {
    find . -depth -name "*$1*" -exec bash -c 'for f; do base=${f##*/}; mv -- "$f" "${f%/*}/${base//'$1'/'$2'}"; done' _ {} +
}

findreplacefilename popi myrobot
findreplace popi myrobot
findreplace Popi MyRobot
findreplace POPI MYROBOT
```

Then add the necessary code to communicate with your robot via USB/serial/ethernet/etc in the file ``myrobot_hw_interface.cpp``.

## Setting an Initial Position, Using with MoveIt!

If you need your robot to startup at a particular position in simulation, or you would like to use this funcitonality to simulate your robot with MoveIt!, see the downstream package (it depends on this package) [moveit_sim_controller](https://github.com/davetcoleman/moveit_sim_controller)

## Other Helper Tools

### Recording to CSV

Write the commands from a trajectory controller to csv file

    rosrun popi_control controller_to_csv SAVE_TO_FILE_PATH CONTROLLER_STATE_TOPIC TIME_TO_RECORD

### Commanding from CSV

Read from csv file and execute on robot

    rosrun popi_control csv_to_controller READ_FROM_FILE_PATH CONTROLLER_STATE_TOPIC TIME_TO_RECORD

### Commanding from Keyboard

Joint-level teleop from a keyboard (TODO: remove had coded topic names)

    rosrun popi_control keyboard_teleop

## Limitations

 - Does not implement estops, transmissions, or other fancy new features of ros_control
 - Does not have any hard realtime code, this depends largely on your platform, kernel, OS, etc
 - Only position control is fully implemented, though some code is in place for velocity control

## Contribute

Please add features, make corrections, and address the limitations above, thanks!

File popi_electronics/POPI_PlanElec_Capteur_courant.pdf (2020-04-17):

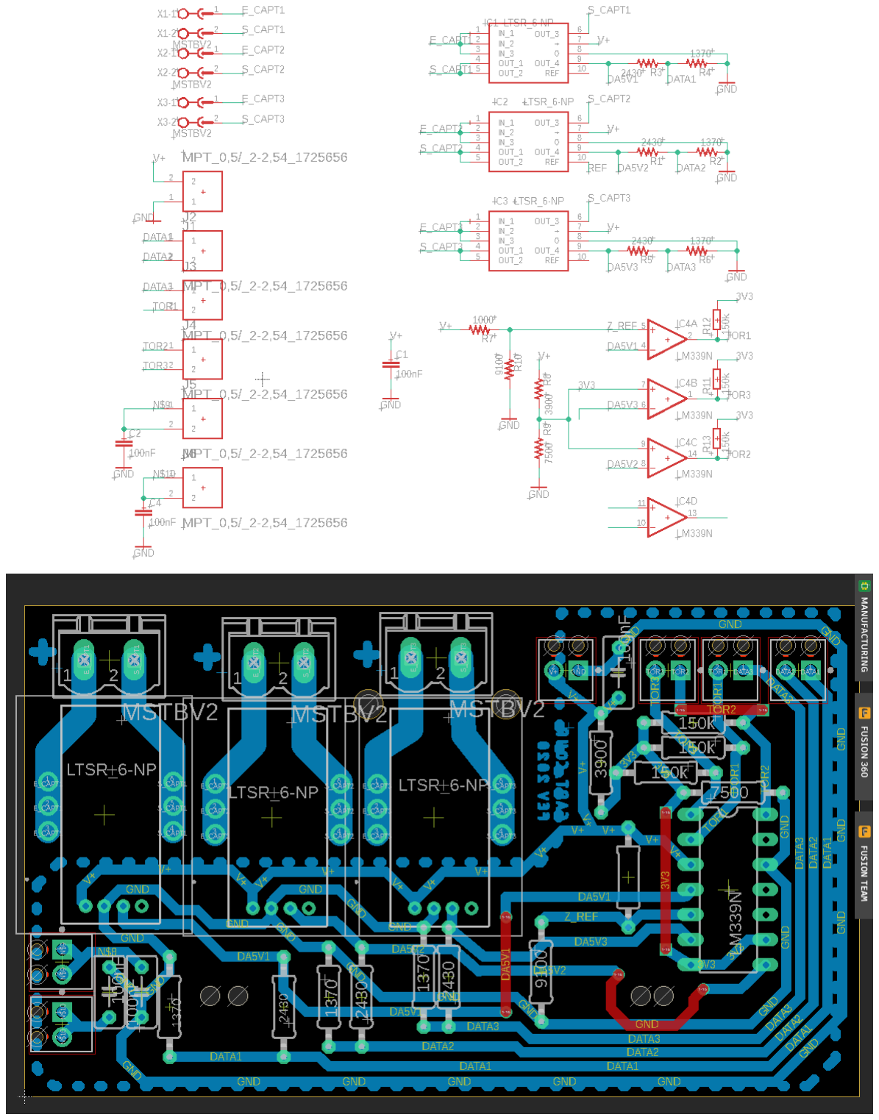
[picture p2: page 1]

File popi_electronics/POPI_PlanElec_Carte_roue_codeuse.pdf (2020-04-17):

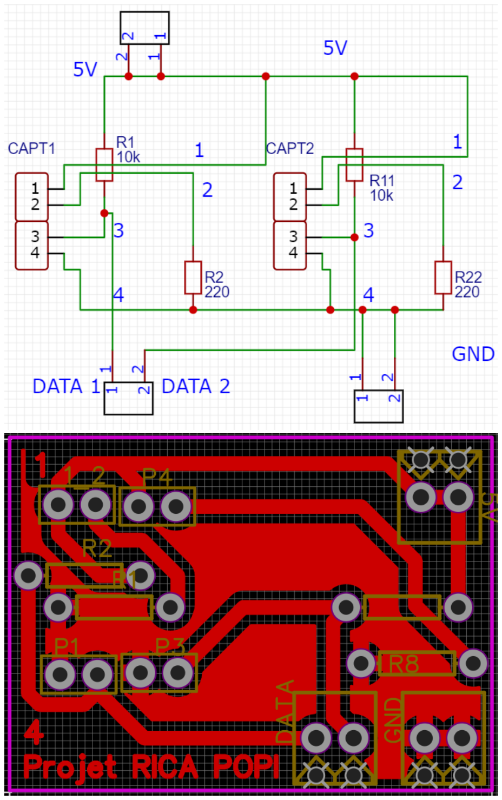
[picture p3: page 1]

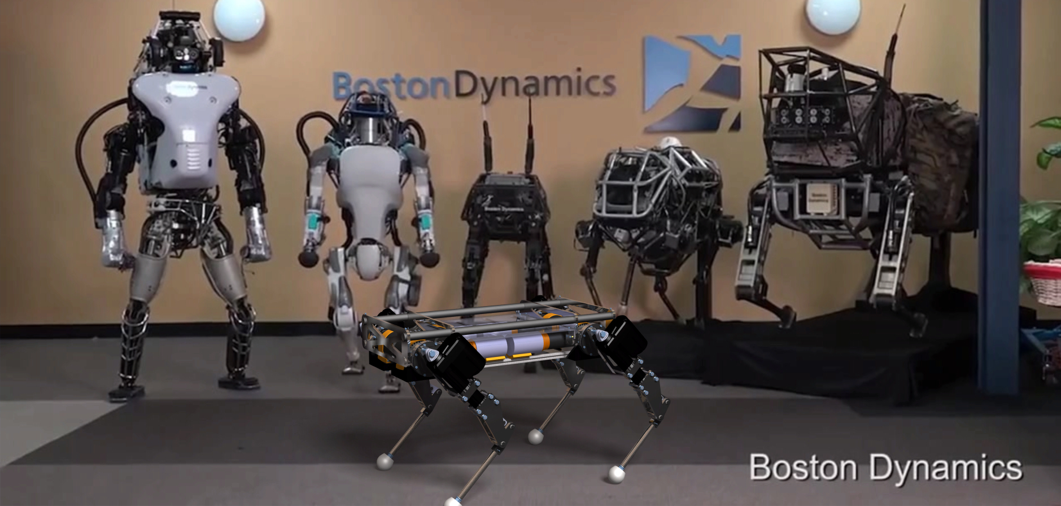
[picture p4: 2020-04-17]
popi_mechanics/3D_renders/Popi wallpaper_01.jpg

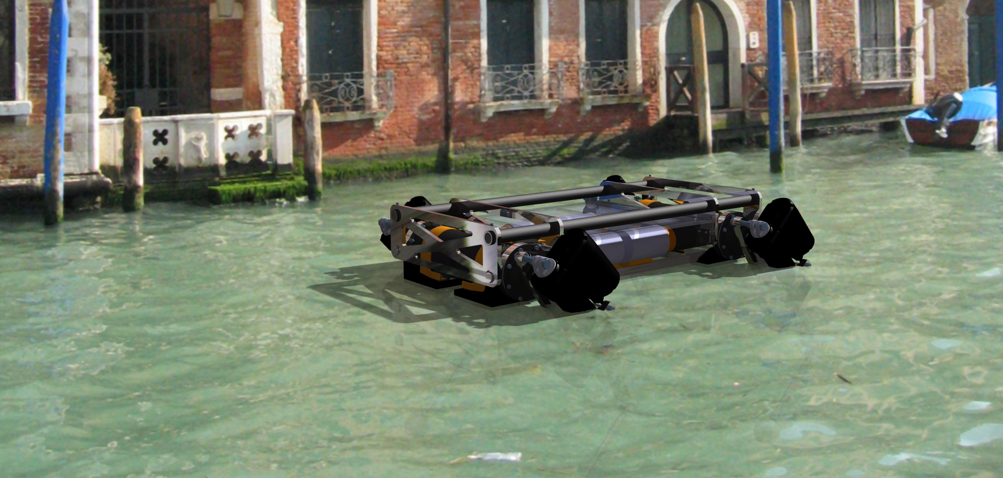
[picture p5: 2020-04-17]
popi_mechanics/3D_renders/Popi wallpaper_09.jpg

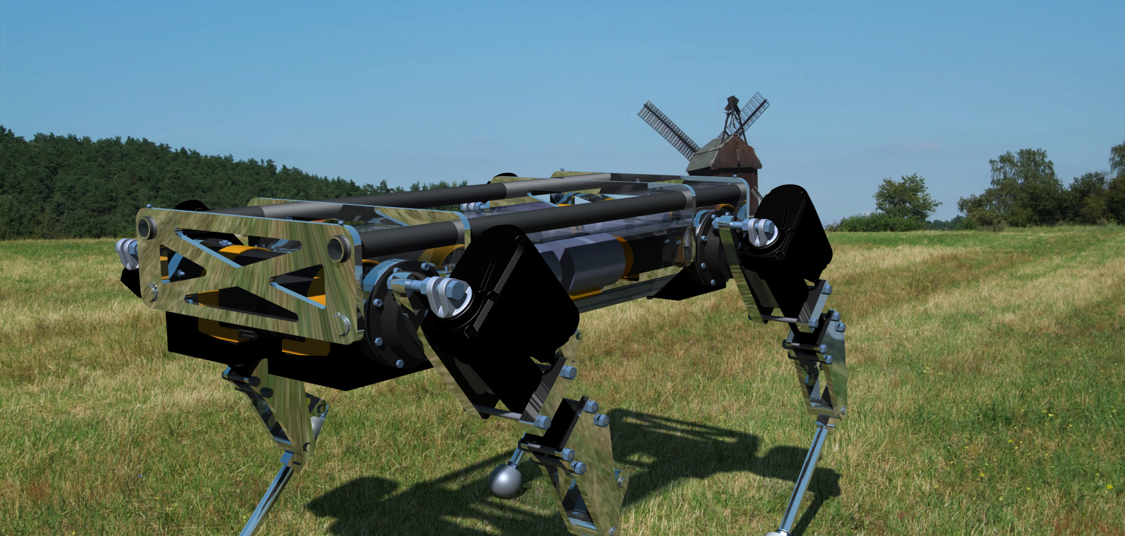
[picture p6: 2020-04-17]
popi_mechanics/3D_renders/Popi wallpaper_07.jpg

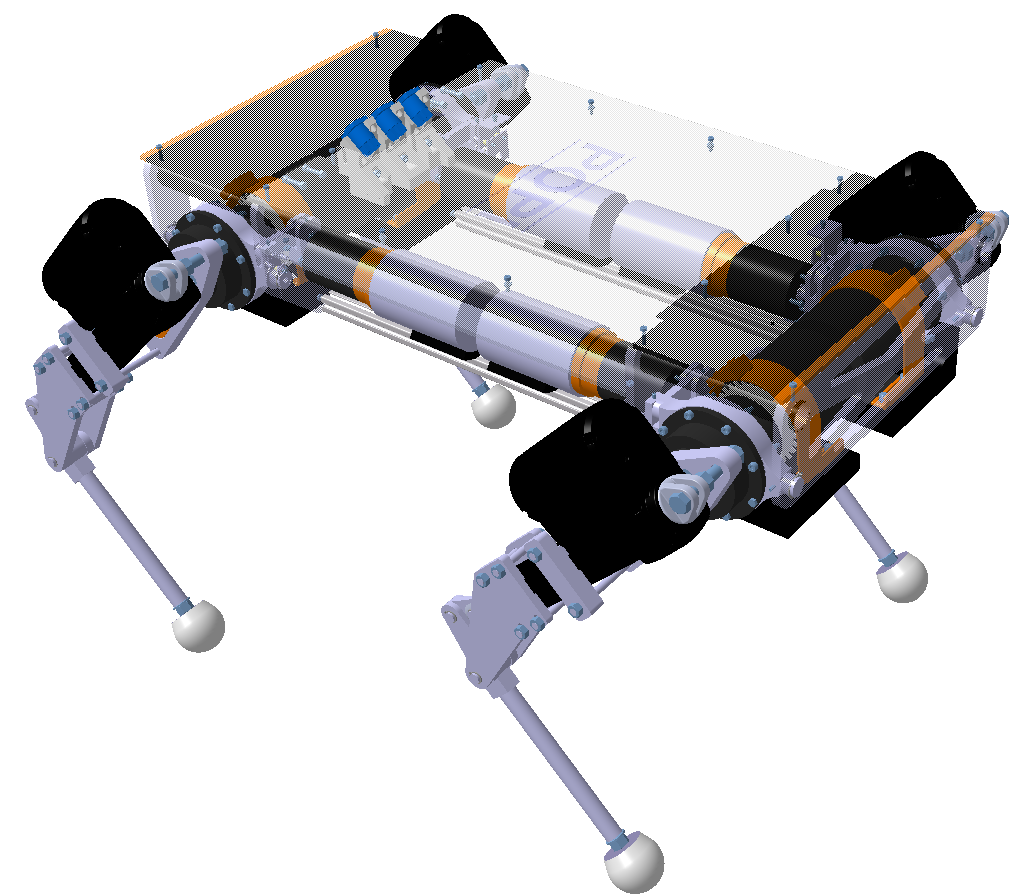
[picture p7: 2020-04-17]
popi_mechanics/3D_renders/Popi transparent actionneurs.png

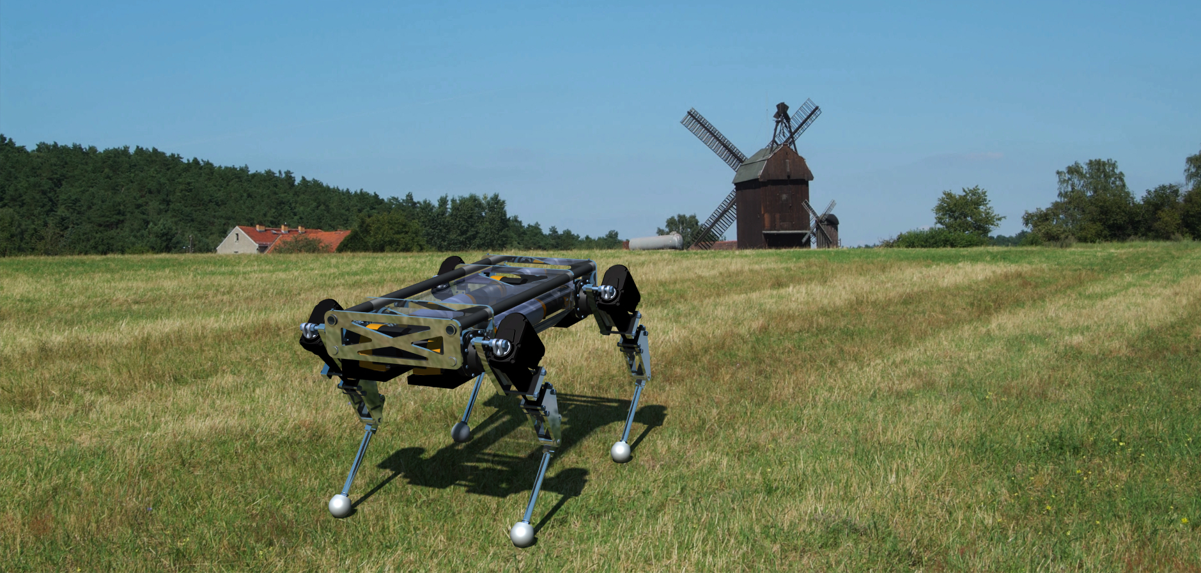
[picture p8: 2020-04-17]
popi_mechanics/3D_renders/Popi wallpaper_06.jpg

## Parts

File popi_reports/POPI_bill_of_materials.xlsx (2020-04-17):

Liste d'achat RICA IV - Groupe 2
Actionneurs | nb | prix unit | prix tot | État de la commande | Données Livraison |  |  | Lien
Vérin MA2 - TiMOTION (prix estimé) | 4 | 200.00 € | 800.00 € | Reçu | Reçu le : 24/10/19 | 3.1 | kg | https://www.timotion.com/fr/product/detail/linear-actuators/ma2-series?upcls=1481269298&guid=1488425822
Moteur épaule MY1016 - 24V - 350W | 4 | 85.50 € | 342.00 € | Reçu | Reçu le : 02/08/19 | 2.53 | kg | http://pocketquadelectrique.csmoto.fr/informations/datasheet2.php
Réducteurs PLFE | 4 | 358.20 € | 1432.80 € | Reçu | Reçu le : 09/09/19 | 3.09 | kg | https://www.neugart.com/fr-fr/sav/outils-et-formations/tec-data-finder/
Moteurs aile - MR977 cbfmotor | 4 | 225.50 € | 902.00 € | Reçu | Reçu le : 24/09/19 | 3.4 | kg | http://www.bernio.it/en/mr-977-64.html
SOUS TOTAL ACTIONNEURS |  |  | 3476.80 € |  |  | 48.48 | kg
Subvention TiMOTION | 1 |  | -800.00 €
TOTAL ACTIONNEURS |  |  | 2676.80 €
Électronique | nb | prix unit | prix tot |  |  |  |  | Lien
Alimentation 24V 40A 1000W | 2 | 50.00 € | 100.00 € | Reçu | Reçu le : 09/09/19 |  |  | https://www.banggood.com/fr/24V-40A-1000W-Switch-Power-Supply-Driver-AC110220V-Regulated-Switching-Power-Supply-for-LED-Strip-p-1323748.html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
Anker Chargeur Secteur USB PowerPort 6 Ports 60W | 1 | 25.99 € | 25.99 € | Reçu | Reçu le : 02/08/19 |  |  | https://www.amazon.fr/Chargeur-Secteur-Anker-PowerPort-Ports/dp/B00PTLSH9G | Pourquoi pas un convertisseur DC 24V / DC 5V avec des résistances ?
Câble USB, longueur 0.5m | 4 | 3.72 € | 14.88 € | Reçu | Reçu le : 09/09/19 |  |  | https://fr.rs-online.com/web/p/cables-usb/1828551/
Boutons arrêt d'urgence | 1 | 19.24 € | 19.24 € | Reçu | Reçu le : 09/09/19 |  |  | https://fr.rs-online.com/web/p/boutons-arret-durgence/7579036/
EMBASE FEM. 4MM NOIR | 16 | 1.27 € | 20.32 € | Reçu | Reçu le : 09/09/19 |  |  | https://fr.rs-online.com/web/p/fiches-bananes/4333332/
Contrôleur Moteur 13A, 5 à 30V, Cytron | 8 | 12.16 € | 97.28 € | Reçu | Reçu le : 09/09/19 |  |  | https://www.robotshop.com/eu/fr/controleur-un-moteur-13a-5-a-30v-cytron.html
Contrôleur Moteur 20A, 6 à 30V Cytron | 4 | 18.16 € | 72.64 € | Reçu | Reçu le : 09/09/19 |  |  | https://www.robotshop.com/eu/fr/controleur-un-moteur-20a-6-30v-cytron.html
Carte micro-SD 32Gb | 3 | 4.99 € | 14.97 € | Reçu | Reçu le : 24/09/19 |  |  | https://fr.shopping.rakuten.com/offer/buy/1934990320/samsung-microsdhc-evo-32go-gb-avec-adaptateur-mb-mc32ga-eu.html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
Encodeur rotatif, Incrémental | 12 | 0.62 € | 7.44 € | Reçu | Reçu le : 09/09/19 |  |  | https://fr.rs-online.com/web/p/codeurs-rotatifs/1814479/
Capteur de courant LTSR, 5 V | 12 | 15.42 € | 185.04 € | Reçu | Reçu le : 09/09/19 |  |  | https://fr.rs-online.com/web/p/transducteurs-de-courant/4995356/
Prise secteur + cable | 1 | 6.00 € | 6.00 € | Reçu | Reçu le : 09/09/19 |  |  | https://fr.rs-online.com/web/p/cordons-electriques/6266616/
Interrupteur de fin de course, Levier à galet, NF/NO, 20 A, 500V | 16 | 8.93 € | 142.88 € | Reçu | Reçu le : 09/09/19 |  |  | https://fr.rs-online.com/web/p/interrupteurs-fin-de-course/8279083/
Câble Ethernet catégorie RJ45 mâle / RJ45 mâle | 2 | 2.24 € | 4.48 € | Reçu | Disponible à la PFM |  |  | https://fr.rs-online.com/web/p/cables-categorie-5e/6572090/
Commutateur, D-Link, DES-1005, 5 ports RJ45 | 1 | 13.60 € | 13.60 € | Commandé | En attente à Thalès |  |  | https://fr.rs-online.com/web/p/commutateurs/1363016/
Fusible 40A | 12 | 0.22 € | 2.64 € | Reçu | Reçu le : 09/09/19 |  |  | https://fr.rs-online.com/web/p/fusibles-auto/7874145/
Cable 24V 40A Rouge | 0 | 21.75 € | 0.00 € | Reçu | Disponible à la PFM |  |  | https://fr.rs-online.com/web/p/fil-de-cablage-electrique/7482137/
Cable 24V 40A Noir | 0 | 21.75 € | 0.00 € | Reçu | Disponible à la PFM |  |  | https://fr.rs-online.com/web/p/fil-de-cablage-electrique/7482112/
Cable 5V - 10 couleurs * 25m | 0 | 29.95 € | 0.00 € | Reçu | Disponible à la PFM |  |  | https://www.amazon.fr/Xenterio-Assortiment-commutation-10-bobines-10-couleurs/dp/B072F4GWNL
Ruban isolant en PVC, Noir 33m x 19mm | 1 | 5.40 € | 5.40 € | Reçu | Reçu le : 09/09/19 |  |  | https://fr.rs-online.com/web/p/rubans-isolants/4089518/
Quadrature encoder counter - 2* STM version | 2 | 16.20 € | 32.41 € | Reçu | Reçu le : 12/11/19 |  |  | https://www.ebay.fr/itm/Quadrature-Encoder-Counter-32-bit-SPI-Interface-for-Raspberry-PI-and-Arduino/382570490376
Accéléromètre PModNav | 1 | 26.98 € | 26.98 € | Reçu | Reçu le : 12/11/19 |  |  | https://fr.farnell.com/digilent/410-326/carte-pmod-barometre-plus-imu/dp/2726217?st=IMU
Potentiomètre rotatif 1kΩ | 4 | 5.40 € | 21.60 € | Reçu | Reçu le : 12/11/19 |  |  | https://fr.farnell.com/bourns/93r1a-r22-a10l/potentiometre-lineair-1k-10-2w/dp/2321802
Phototransistor | 8 | 0.00 € | 0.00 € | Reçu | Disponible à la PFM |  |  | https://fr.farnell.com/sharp/gp1s58vj000f/optocommutateur/dp/9708073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
SOUS TOTAL ÉLECTRONIQUE |  |  | 813.79 €
Subvention Thalès | 1 |  | -421.92 €
TOTAL ÉLECTRONIQUE |  |  | 391.87 €
Intelligence embarquée | nb | prix unit | prix tot |  |  |  |  | Lien
Raspberry pi 3 b+ | 1 | 31.18 € | 31.18 € | Commandé | En attente à Thalès |  |  | https://fr.rs-online.com/web/p/products/1373331/
BeagleBone Black | 2 | 57.00 € | 114.00 € | Reçu | Reçu le : 09/09/19 |  |  | https://fr.rs-online.com/web/p/products/1252411/
SOUS TOTAL INTELLIGENCE EMBARQUE |  |  | 145.18 €
Subvention Thalès | 1 |  | -145.18 €
TOTAL INTELLIGENCE EMBARQUÉE |  |  | 0.00 €
Matière | nb | prix unit | prix tot |  |  |  |  | Lien
Plaque Alu 20mm - 50*50 | 1 | 140.60 € | 140.60 € | Reçu | Disponible à la PFM
Plaque Alu 10mm - 70*85 | 1 | 210.73 € | 210.73 € | Reçu | Disponible à la PFM |  |  |  | (2,5 d'épaisseur n'existe pas sur le site en question)
Plaque Alu 8 mm - 50*17 | 1 | 112.70 € | 112.70 € | Reçu | Disponible à la PFM
Rond de 20 mm - L = 1346 mm | 1 | 43.88 € | 43.88 € | Reçu | Disponible à la PFM
Tube Rond de 20mm (Thalès) | 1 | 60.00 € | 60.00 € | Reçu | Reçu le 09/09/19
Tube Elcom profilés 20*20 | 1 | 31.79 € | 31.79 € | Reçu | Disponible à la PFM
Tige filetées 1000mm de M5, M8, M12 | 1 | 4.70 € | 4.70 € | Reçu | Disponible à la PFM
Palier SKF - PCMF 202311.5 E | 4 | 3.04 € | 12.16 € | Reçu | Reçu le : 12/11/19 |  |  | https://www.orexad.com/fr/palier-lisse-coussinet-paliers-lisses-paliers-lisses-spheriques/p-G1321009446
SOUS TOTAL MATIÈRE |  |  | 616.56 €
Subvention Thalès | 1 |  | -60.00 €
TOTAL MATIÈRE |  |  | 556.56 €
Cout total sans subvention |  |  | 5052.33 €
Subvention |  |  | -1427.10 €
COUT TOTAL |  |  | 3625.23 €
Budget restant |  |  | 374.77 €
Pourcentage du budget restant |  |  | 9.36925%

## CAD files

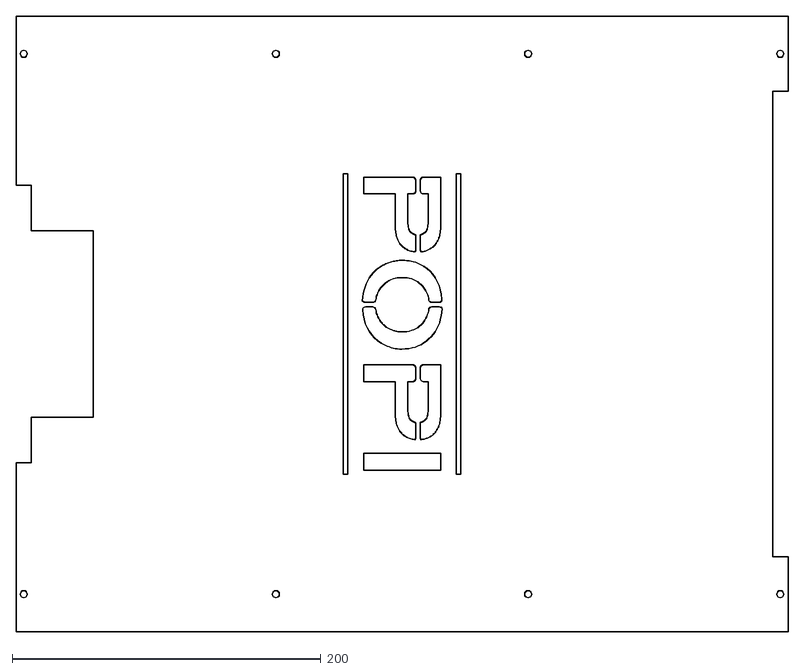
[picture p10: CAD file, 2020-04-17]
popi_mechanics/CATIA/Plexi trans 2.dxf
500.0 x 398.5

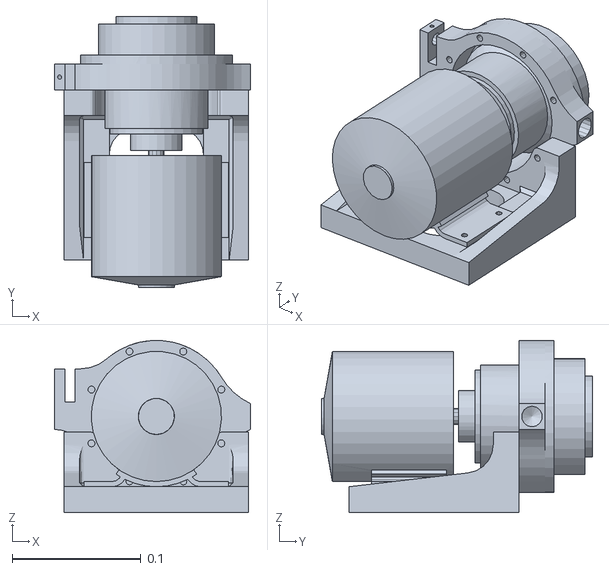
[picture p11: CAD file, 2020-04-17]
popi_software/popi/popi_description/meshes/EpauleAVG.STL
0.152 x 0.21 x 0.133

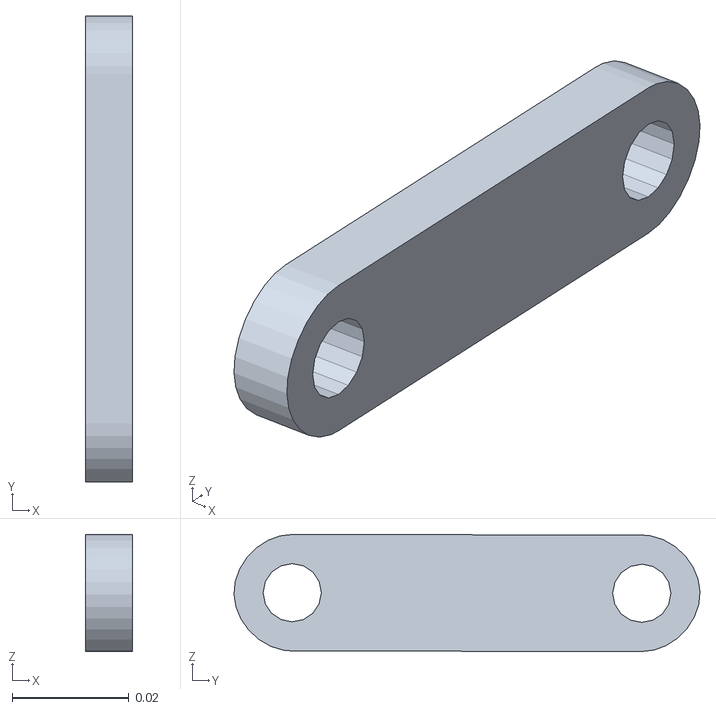
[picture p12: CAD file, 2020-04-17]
popi_software/popi/popi_gazebo/popiv10/meshes/BieletteAileArG_col.STL
0.008 x 0.08 x 0.0201

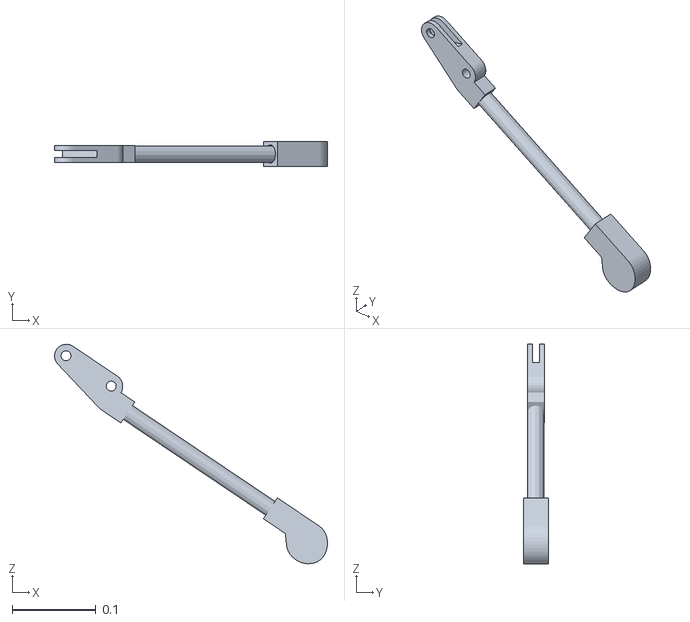
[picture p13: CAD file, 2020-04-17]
popi_software/popi/popi_gazebo/popiv9/meshes/BJambeArG.STL
0.326 x 0.03 x 0.262

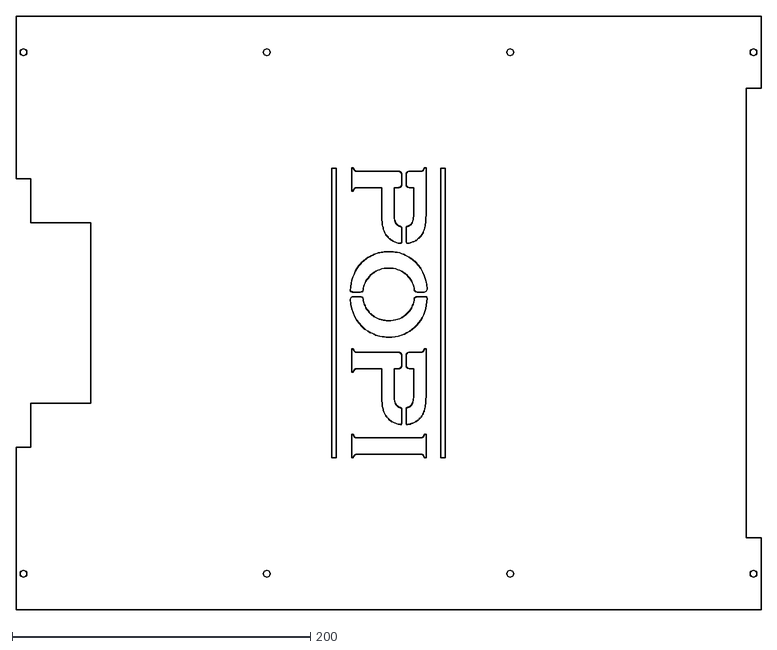
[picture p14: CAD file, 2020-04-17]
popi_mechanics/CATIA/Plexi trans.dxf
500.0 x 398.5

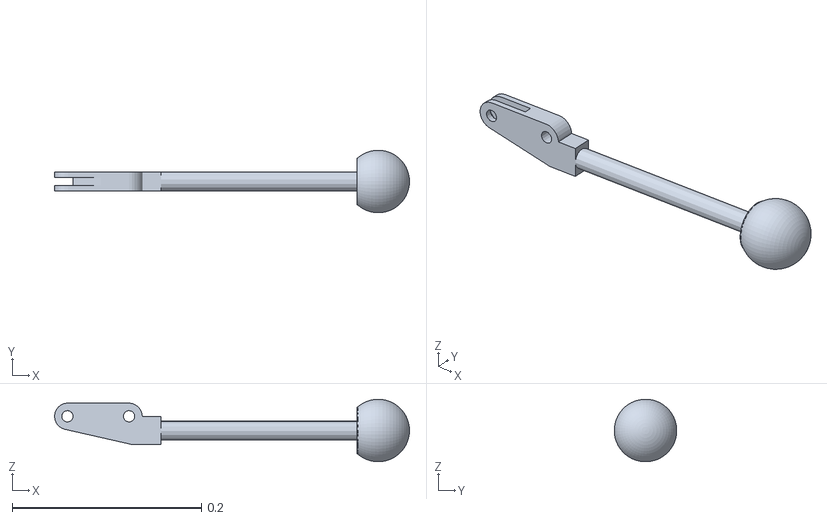
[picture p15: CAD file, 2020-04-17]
popi_software/popi/popi_description/meshes/BJambeAVG.STL
0.375 x 0.066 x 0.066

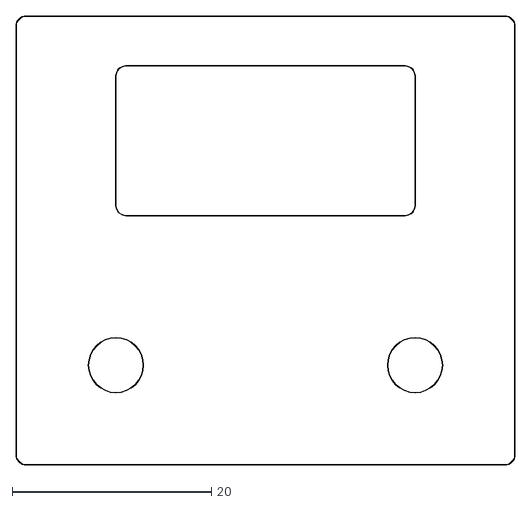
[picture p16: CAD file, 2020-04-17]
popi_mechanics/CATIA/Crochet for dxf.dxf
50.0 x 45.0

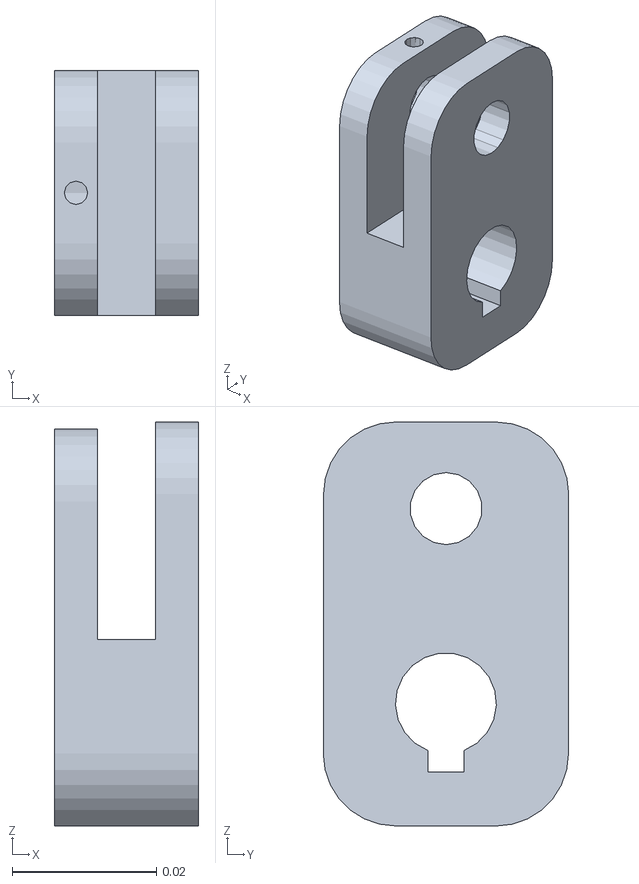
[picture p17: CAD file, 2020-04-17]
popi_software/popi/popi_gazebo/popiv9/meshes/AileArG.STL
0.02 x 0.034 x 0.056

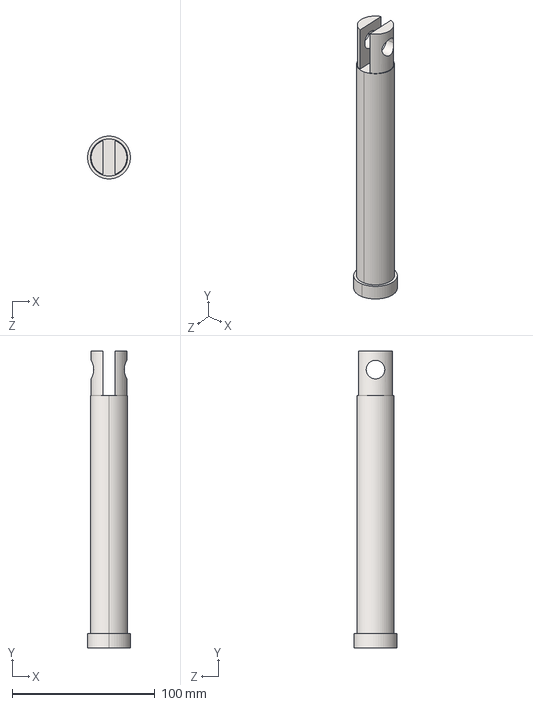
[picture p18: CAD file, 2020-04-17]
popi_mechanics/CATIA/Tige vérin.STEP
30.0 x 208.0 x 30.0 mm

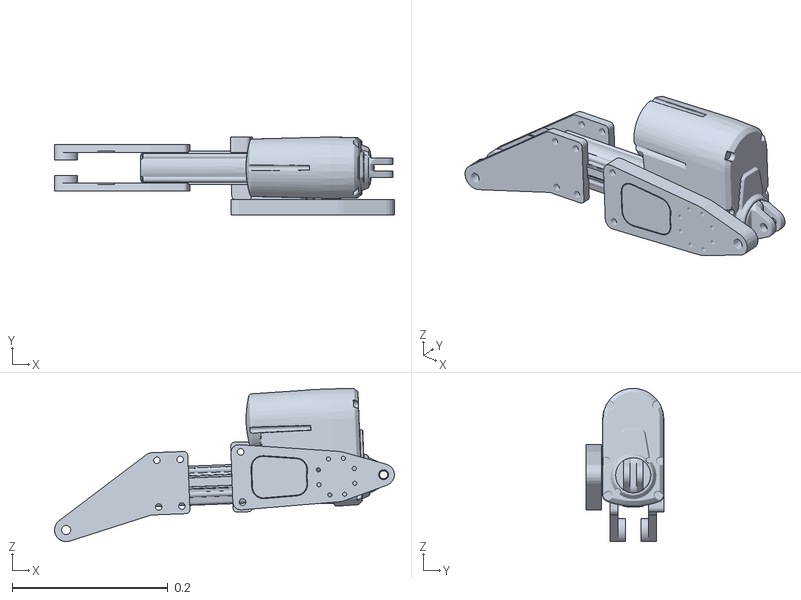
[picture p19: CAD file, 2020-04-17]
popi_software/popi/popi_description/meshes/HJambeARG.STL
0.437 x 0.1 x 0.197

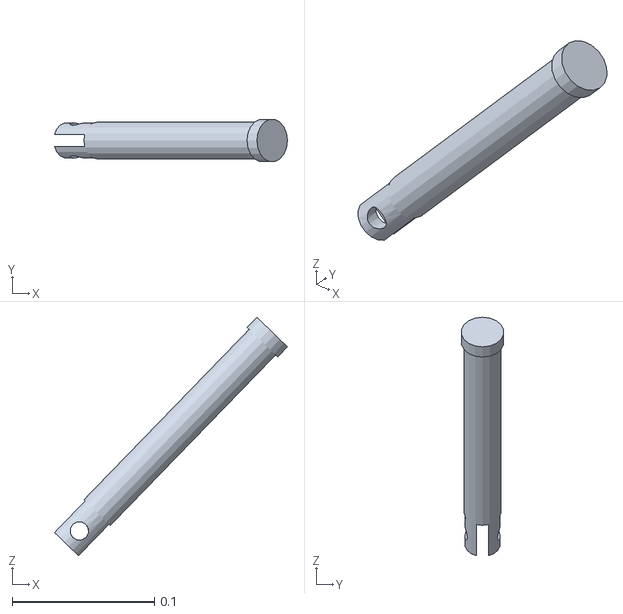
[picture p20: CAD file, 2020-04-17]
popi_software/popi/popi_gazebo/popiv10/meshes/TigeVerinAvD_col.STL
0.164 x 0.0295 x 0.168

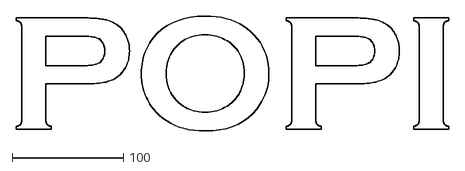
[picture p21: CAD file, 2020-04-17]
popi_mechanics/CATIA/Popi texte.dxf
389.2 x 103.5

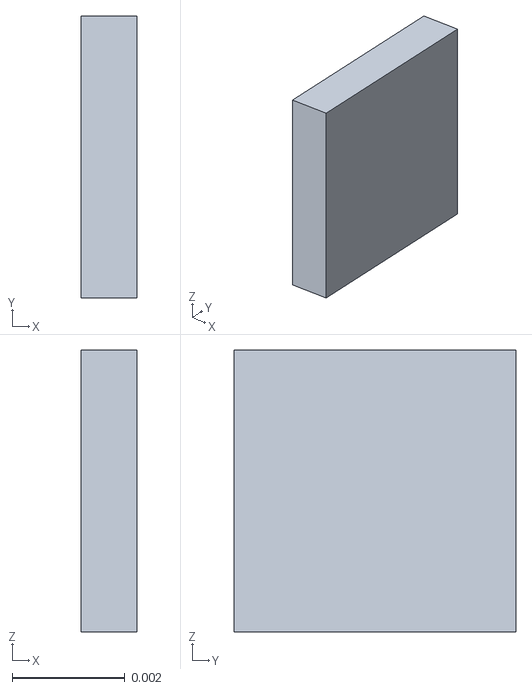
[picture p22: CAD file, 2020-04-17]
popi_software/popi/popi_description/meshes/PiedARD.STL
0.001 x 0.005 x 0.005

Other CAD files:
popi_software/popi/popi_gazebo/popiv10/meshes/EpauleArD_col.STL
popi_software/popi/popi_gazebo/popiv9/meshes/BieletteAileAvG_col.STL
popi_software/popi/popi_description/meshes/BJambeARD.STL
popi_software/popi/popi_gazebo/popiv10/meshes/BJambeAvD_col.STL
popi_software/popi/popi_gazebo/popiv9/meshes/TigeVerinAvD_col.STL
popi_mechanics/CATIA/07330-201200.CATPart
popi_mechanics/CATIA/10_37_0505_0250_001.CATPart
popi_mechanics/CATIA/210217-3x10.CATPart
popi_mechanics/CATIA/7940012.CATPart
popi_mechanics/CATIA/Autonomous POPI Text.dxf
popi_mechanics/CATIA/Axe bloquant porte-reducteur 2.CATPart
popi_mechanics/CATIA/Axe bloquant porte-reducteur.CATPart
popi_mechanics/CATIA/Axe coude 2.CATPart
popi_mechanics/CATIA/Axe coude verin.CATPart
popi_mechanics/CATIA/Axe coude.CATPart
popi_mechanics/CATIA/Bague reducteur.CATPart
popi_mechanics/CATIA/Bielette aile.CATPart
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

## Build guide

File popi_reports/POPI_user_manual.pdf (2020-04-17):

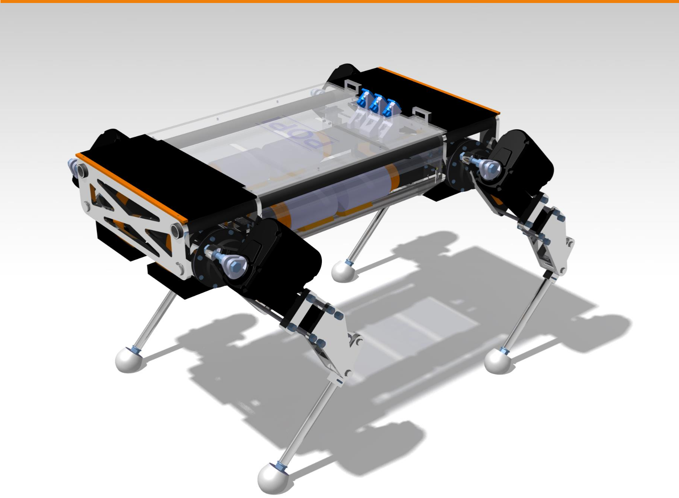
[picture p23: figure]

# POPI

# Prototype RICA IV

# 2020 | Par : MKX3

## L’équipe ayant participé à ce projet est composée de :

### Aharram Gutton Anaïs

### Brottet Karla

### CombacalRémi

### Graton Clémence

### Labarussiat Lucas

### Oddon Yannis

### Pelloux-Prayer Jean

### Peres Olivier

### Rougé Guillaume

### Thomaso Clément

### Tichit Pascal

SOMMAIRE

8.1 | PRESCRIPTION GENERALE DE SECURITE | 31
8.2 | TRANSPORT | 32
8.3 | INSTALLATION / DESINSTALLATION | 32
8.4 | MAINTENANCE | 32
8.4.1 INSTRUCTIONS DE MAINTENANCE PREVENTIVE | 34
8.4.2 INSTRUCTIONS DE MAINTENANCE CORRECTIVE | 34
ANNEXE 1 : PLANS DE MONTAGE ELECTRONIQUE | 37
ANNEXE 2 : NOTICE DE MONTAGE MECANIQUE | 41

TABLE DES FIGURES
Figure 1 : Dimensions du robot POPI | 4
Figure 2 : Les différents types d'actionneurs | 5
Figure 3 : Axe de symétrie POPI | 6
Figure 4 : Electronique de la partie commande | 8
Figure 5 : Schéma de la platine d'alimentation | 9
Figure 6 : Distribution de l’alimentation | 10
Figure 7 : Architecture réseau du robot | 13
Figure 8 : Schéma de fonctionnement logiciel de POPI | 15
Figure 9 : Arborescence des dossiers | 16
Figure 10 : Branchement de l'ombilic | 18
Figure 11 : Interface utilisateur Towr | 19
Figure 12 : Interface Rviz | 20
Figure 13 : Sélection des topics sur rqt_bag | 21
Figure 14 : Fenêtre rqt_bag pendant l'enregistrement | 22
Figure 15 : Configuration de la manette | 23
Figure 16 : Interface rqt_gui – message publisher (1), topic monitor (2) et dynamic reconfigure (3) .. 24
Figure 17 : Interface rqt_plot | 25
Figure 18 : Utilisation des poignées de manutention | 26
Figure 19 : Page de paramétrage réseau | 26
Figure 20 : Page de paramétrage de la connexion filaire | 27
Figure 21 : Onglet détail de la page de paramétrages de la connexion filaire | 27
Figure 22 : POPI en position repos | 29
Figure 23 : POPI en position nominale | 30
Figure 24 : Positionnement du socle | 31
Figure 25 : Ajout d'une connexion par pont | 35
Figure 26 : Sélection de l'interface à asservir | 36
Figure 27 : Vérification de paramètres réseaux | 36

TABLE DES TABLEAUX
Tableau 1 : Caractéristiques du robot POPI | 6
Tableau 2 : Caractéristiques de l’ensemble épaule | 7
Tableau 3 : Caractéristiques de l’ensemble aile | 7
Tableau 4 : Caractéristiques de l’ensemble coude | 8
Tableau 5 : Code couleur des fils électriques du robot | 11
Tableau 6 : Affectation des bornes BeagleBoneBlack Gauche | 12
Tableau 7 : Affectation des bornes BeagleBoneBlack Droite | 12
Tableau 8 : Nomenclature des composants électronique | 38

FI GU R E 1 : DI MENSI ON S DU R OBOT

## 1 Préambule

Le produit POPI est proposé par les MKX3 - Groupe 2 en réponse au cahier des charges rédigé par MM. P. GIRONES & V. CHAPURLAT, daté du 19/01/2016, réf : DPAD/CP2NAPM/CC/2016-01b.

Le produit est un robot quadrupède dont les caractéristiques techniques ont été choisies dans le cadre de la montée en gamme du RICA III. Le produit POPI a été conçu pour franchir un palier et une fosse de 30cm, ainsi qu’une configuration escalier (Giron 28cm).

Dans l’état, POPI est un prototype de niveau TRL 6 (Démonstration du modèle système / sous-système ou du prototype dans un environnement significatif) du sous-système base mobile du robot RICA.

Le robot RICA a pour cible des missions de collecte de données radiologiques, dimensionnelles et visuelles dans des milieux sévères. L’interface opérateur du prototype a été développée afin de rendre POPI pilotable par un technicien de niveau BAC+2. Dans ce dossier constructeur, vous retrouverez toutes les informations nécessaires à la mise en fonctionnement, à l’utilisation, au transport et à la maintenance du produit POPI.

Note : l'ensemble de nos travaux, comprenant ce dossier constructeur, les plans électroniques et mécaniques ainsi que les codes sources, sont disponibles en open-source (sous licence BSD-3) sur le GitHub (https://github.com/popi-mkx3/popi_ros) du projet.

## 2 Description générale

## 2.1 Description physique du robot

Le produit POPI est un robot quadrupède. L’alimentation du robot se fait via un ombilic, relié à un tableau d’alimentation qui est raccordé au secteur.

Le poids de l’ensemble est de 70 kg,

Le robot POPI, présenté en Figure 1, en position nominale, possède les dimensions générales

suivantes : 1017mm x 662mm x 620mm (PxLxH).

## 2.2 Description des accessoires

2.2.1 Socle
Un support à roulettes a été conçu afin de faciliter le déplacement du robot POPI sur de courtes distances et sur un même niveau.

C’est aussi son support de stockage. Lorsque le robot est éteint, il doit être positionné sur ce socle.

2.2.2 Poignées
Lorsque le robot doit être déplacé alors qu’il n’est pas sur son socle, des poignées sont à disposition.

## Voir 7.7.1 Mode opératoire de manutention

2.2.3 Pieds
Plusieurs types de pieds sont disponibles, en fonction de l’état du sol. Les pieds du premier sont souples, pour permettre une surface de contact maximale. Les pieds du second lot sont rigides, il est adapté à un sol abrasif. Ils sont très facilement interchangeables.

## 2.3 Description du fonctionnement du robot

L’ensemble des choix de conception ont été réalisés dans le but de satisfaire aux exigences de franchissement définies dans le cahier des charges. Pour rappel, ces exigences sont le franchissement d’un palier de 30cm, d’une fosse de 30 cm ainsi qu’un escalier avec un giron de 28cm.

Le produit POPI est composé de 12 actionneurs, 3 par p atte (voir partie 3.1 Descriptif de
l’équipement.).

L’association des actionneurs « épaule » et « coude » permet la marche linéaire du robot. L’action de « l’aile » permet au robot de tourner.

FI GU R E 2 : LES D I FF ER ENTS TYPES D 'AC TION NEUR S

## 2.4 Caractéristiques techniques du robot POPI

Vitesse | Marche statique : 0,2 m/s | Marche dynamique : 0,5 m/s
Poids | 70 kg
Charge utile transportable | 20kg
Encombrement (PxLxH) | 1017mm x 662mm x 620mm
Raccordement électrique | 1 x 220V / 50 Hz / 16A
Consommation électrique max | 2000W
Portée de l’ombilic | 10 m
Nombre d’actionneurs par patte | 3
Degrés de liberté | 18 DDL
Boitier de commande | Manette de Xbox & ordinateur externe
Alimentation interne des actionneurs | 2x24V avec limitation 2x40A
Niveau sonore | 60dB
Matériaux | Aluminium, Acier, PLA, ABS, Silicone
Température de fonctionnement | -20 → 45° C

TABLEAU 1 : CAR AC TER ISTIQU ES DU ROBOT POPI

## 3 Partie mécanique

## 3.1 Descriptif de l’équipement

Le robot POPI possède un axe de symétrie longitudinal. Il possède 4 pattes , identiques 2 à 2.

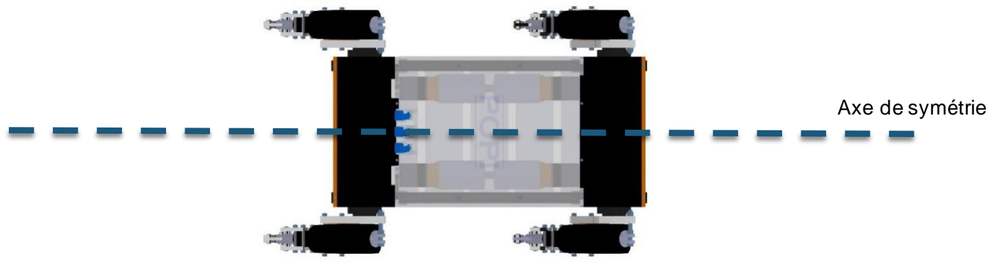
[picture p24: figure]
Axe de symétrie

Chaque patte est composée d’une articulation de type « épaule », d’une articulation de type « aile » et d’une articulation de type « coude ». Chacune de ces articulations correspond à un actionneur.

On compte donc 12 actionneurs :

- Épaule : 4 moteurs (couplés à des réducteurs)
- Aile : 4 motoréducteurs
- Coude : 4 vérins

Pour une nomenclature complète des pièces, se référer à l’ Annexe 2 : Notice de montage
mécanique.

FI GU R E 3 : AXE D E SYM ETR IE POPI

3.1.1 Actionneur épaule

Moteur – Réducteur épaule

Référence | MY1016 - CSMOTO
Alimentation | 24 V DC
Puissance | 350 W
Courant max | 18,7 A
Réducteur | PLFE 90 - NEUGART
Rapport de réduction | 100
Vitesse max sans charge | 34,5 tr/min
Couple max sans charge | 300 Nm
Vitesse max avec charge | 27,5 tr/min
Couple max avec charge | 122 Nm
Plages d’articulations épaule | [0; 180] degré, soit [0 ; π] rad

TABLEAU 2 : CAR AC TER ISTIQU ES DE L’EN SEMBLE EPAULE

3.1.2 Actionneur aile

Motoréducteur aile

Référence | MR 977 – CBF MOTOR
Alimentation | 24 V DC
Puissance | 130 W
Courant max | 20 A
Rapport de réduction | 96
Longueur | 229 mm
Vitesse max sans charge | 30 tr/min
Vitesse max avec charge | 26 tr/min
Couple max avec charge | 120 Nm
Plages d’articulations aile | [−22; 22] degré soit [−0,4 ; 0,4] rad

TABLEAU 3 : CAR AC TER ISTIQU ES DE L’EN SEMBLE AILE

3.1.3 Actionneur coude
Vérin coude
Référence | MA2 - TiMOTION
Alimentation | 24V DC
Puissance | 200 W
Vitesse max sans charge | 28,5 mm/s
Vitesse max avec charge | 22,0 mm/s
Charge de poussée | 2000 N
Force de verrouillage automatique | 2600 N
Duty cycle | 25 %
Courant sans charge | 2,2 A
Courant avec charge | 9.0 A
Plages d’articulations coude | [15; 125] degré soit [0,2 ; 2,2] rad

TABLEAU 4 : CAR AC TER ISTIQU ES DE L’EN SEMBLE COU DE

## 3.2 Principe de montage

Une nomenclature détaillée et une notice de montage sont présentées en Annexe 2 : Notice
de montage mécanique.

## 4 Partie électronique

L’ensemble des éléments électroniques est fixé sur une plaque en plexiglas disposée au-dessus dans le corps du robot. On retrouve dans le positionnement des éléments une symétrie droite / gauche comme pour la partie mécanique. On distingue la partie commande (au centre de la plaque), de la partie puissance (en dehors de la plaque). Le lien entre ces deux parties se fait par les cartes « contrôleur » Cytron 13A et 20A placées aux extrémités avant et arrière de la plaque.

## 4.1 Intelligence embarquée

Le robot embarque une carte Raspberry PI 3B+ et deux cartes BeagleBoneBlack (BBB). La Raspberry PI est utilisée pour sa puissance de calcul tandis que les BBB sont utilisées pour leur nombre d’entrées / sorties. Chaque BBB s’occupe de la lecture des capteurs et de l’écriture des commandes

FI GU R E 4 : ELEC TR ONIQU E DE LA PAR TIE C OMM AN DE moteurs PWM pour l’un des deux côtés du robot. Les actionneurs de l’aile et du coude sont commandés par des cartes contrôleur 13A et les actionneurs de l’épaule par des cartes contrôleurs 20A.

## 4.2 Capteurs

25 capteurs sont présents sur le robot POPI. On retrouve tout d’abord une centrale inertielle, située sur la plaque en plexiglas supportant la partie électronique.

Ensuite sont situés sur chaque patte :

- Une roue codeuse placée entre le moteur et le réducteur de l’épaule. C’est un capteur de position relative, qui nous permet de connaitre l’angle de l’épaule. Il est contrôlé par les QEC.
- Un capteur de position situé au niveau de l’aile.
- Une sortie capteur provenant du vérin.

Pour chaque actionneur il y a un capteur de courant, qui permet d’être informé en cas d’appel de courant trop important.

## 4.3 Alimentation

4.3.1 Platine d’alimentation
La platine d’alimentation, présentée en Figure 5, fournit l’alimentation au robot. Elle permet l’alimentation directe en 230V AC, et la transformation du 230 V AC en 24V DC par deux sources distinctes situées à l’arrière de la platine.

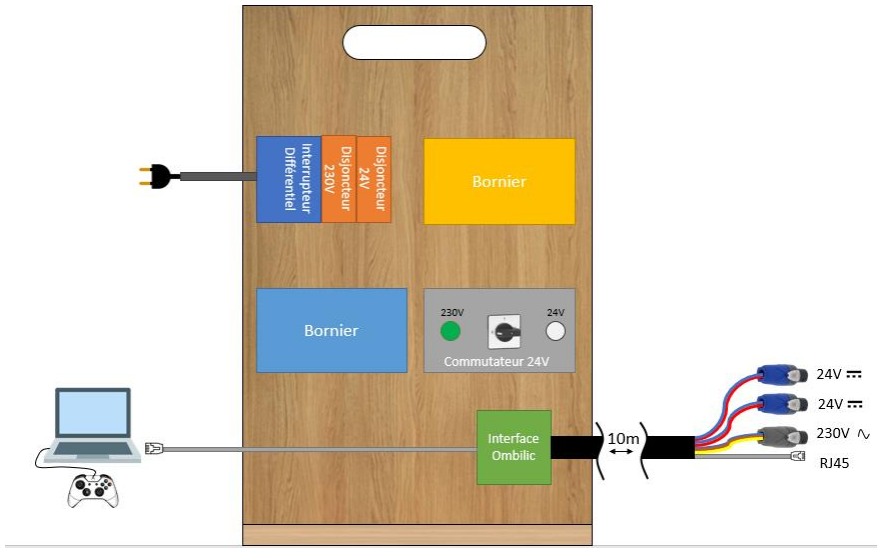
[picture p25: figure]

FIGU R E 5 : SC H EM A DE LA PLATI NE D 'ALIMEN TATI ON

L’ombilic, qui regroupe les différents câbles d’alimentation et de communication dans une seule gaine est relié d’une part à la platine d’alimentation et de l’autre part au robot.

4.3.2 Distribution de l’alimentation
A l’extrémité de l’ombilic coté robot, on trouve :
- 2 connecteurs d’alimentation 24V DC
- 1 connecteur d’alimentation 230V AC
- Un câble RJ45
- 2 mousquetons

Il permet d’alimenter les actionneurs, les cartes électroniques, les capteurs. Il permet aussi la communication avec le PC utilisateur et possède deux mousquetons pour éviter de tirer sur les câbles. Les mousquetons peuvent aussi permettre de tirer le robot hors de sa zone de mission si nécessaire.

Le 24V DC est dédié à la partie puissance. Il est relié aux cartes « contrôleur » qui délivrent la puissance aux actionneurs.

Le 230V AC est transformé en 5V DC et est distribué à la Raspberry PI, aux BBB, aux capteurs de courant et aux cartes Quadrature Encoder Counter (QEC) via un hub USB.

Les deux BeagleBoneBlack fournissent une tension de 1,8V utilisée pour alimenter les capteurs de positions de type potentiomètre du coude et de l’aile.

FI GU R E 6 : DI STR IBU TION DE L’ALI MENTATI ON

## 4.4 Gestion du câblage

4.4.1 Code couleur

TABLEAU 5 : COD E C OU LEU R D ES FI LS ELEC TRI QUES DU R OBOT

4.4.2 Affectation des bornes
BeagleBoneBlack Gauche

TABLEAU 6 : AF F EC TATI ON D ES BOR NES BEAGLEBON EBLACK GAU CH E
BeagleBoneBlack Droite

TABLEAU 7 : AF F EC TATI ON D ES BOR NES BEAGLEBON EBLACK DROITE

## 4.5 Montage de l’électronique

Une nomenclature détaillée et des plans de montages sont présentés en Annexe 1 : Plans de
montage électronique.

## 5 Réseau

Le réseau a été configuré de la façon suivante :

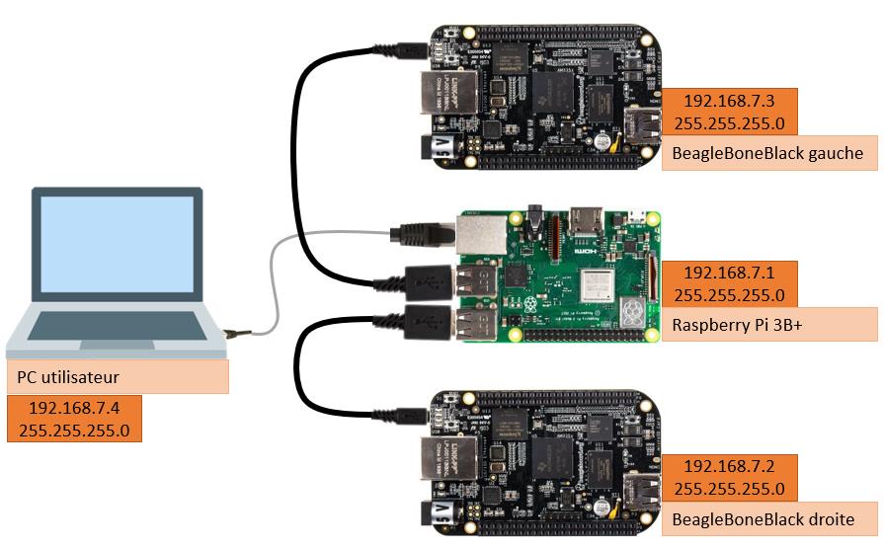
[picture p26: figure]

Toutes les adresses IP sont configurées en statique. Les ports USB de la Raspberry et micro USB des BeagleBoneBlack sont utilisés comme des ports Ethernet. Un pont réseau relie les 3 interfaces réseau de la Raspberry (2 USB et 1 Ethernet) sous l’adresse 192.168.7.1.

Sur chaque carte des serveurs SSH ont été ouvert.

## 6 Architecture logicielle

L’ensemble de l’architecture logicielle de POPI a été créée sur ROS. ROS, p our Robot Operating System, (https://www.ros.org/) est un middleware qui est devenu un standard dans la conception robotique. C’est lui qui assure la communication entre l’ensemble de nos logiciels, ou plutôt l’ensemble de nos nœuds, à savoir des programmes (en Python ou C++) que nous avons transformés en exécutables.

## 6.1 Principe de fonctionnement

Pour le moment, le produit fonctionne en deux temps qu’il se faut de bien distinguer :

- La génération de la trajectoire de marche
- L’envoi de cette trajectoire sur le robot

En effet, le produit ne dispose pas à l’heure actuelle d’une génération de trajectoire de marche à la volée. Ce fonctionnement en deux étapes distinctes permet de s’assurer que les commandes envoyées sur le robot soient correctes et ainsi de diminuer le risque de chute du robot.

FI GU R E 7 : AR C HITEC TU RE R ESEAU DU ROBOT

Le produit est fourni avec des trajectoires de marche qui ont été testées et validées par nos équipes, mais aussi avec l’ensemble des outils nécessaires à la génération de vos propres trajectoires. En cela, POPI se veut être une plateforme de développement ouverte pour le client.

Dans la suite de cette partie, nous présenterons ces différents outils. Si vous souhaitez connaître immédiatement les instructions pour les utiliser, vous pouvez vous référer à la partie 7 Notice d’instruction.

## 6.2 Génération de trajectoire

C’est durant cette étape que vont être calculées l’ensemble des commandes à envoyer sur les 12 actionneurs pour réaliser une marche. Pour ce faire, nous utilisons le package ROS Towr (https://github.com/ethz-adrl/towr) développé par Alexander W. Winkler.

Les modèles cinématique et dynamique de notre robot y ont été ajoutés, indiquant notamment les positions nominales des pieds dans le repère de la base et leur écart maximal à cette position nominale, mais aussi le poids de la base et les composantes de sa matrice d’inertie (selon le modèle du Single Rigid Body Dynamics). (https://www.research-collection.ethz.ch/bitstream/handle/20.500.11850/272432/thesis_winkler.pdf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)

À partir de ces informations et des paramètres de marche définis dans l’application (terrain, position et orientation d’arrivée, démarche souhaitée), le programme calcule les trajectoires de chaque pied au cours de la marche. Avec celles-ci, en utilisant le modèle géométrique inverse du robot, défini dans le package Xpp qui est nécessaire au fonctionnement de Towr, nous calculons les trajectoires que doivent suivre les actionneurs : on obtient nos commandes.

Ces commandes peuvent par la suite être enregistrées en format rosbag à l’aide de l’outil rqt_bag (http://wiki.ros.org/rqt_bag) et éventuellement modifiées sur un tableur, puis simulées avant d’être envoyées sur le robot.

## 6.3 Simulation

Xpp (http://wiki.ros.org/xpp) permet la visualisation 3D sur RViz (http://wiki.ros.org/rviz) du robot lors de la marche, mais également d’autres éléments comme les forces de contact ou encore les cônes de friction.

Le modèle URDF (http://wiki.ros.org/urdf) (Unified Robot Description Format) indispensable à toute visualisation ou simulation du robot fait partie des éléments livrés avec POPI. Celui-ci a été généré directement à partir du modèle 3D mécanique du robot afin de s’assurer de sa représentativité. Il contient, sous forme de texte (XML), l’ensemble des informations des corps composants le robot (forme, dimensions, poids, etc.) et de leurs liaisons (type, limites, élasticité, friction).

Les liaisons ont ensuite été simplifiées pour conserver les mouvements fonctionnels, alléger la simulation et passer outre les problèmes générés par les chaînes cinématiques fermées qui transforment le mouvement de translation du vérin en rotation du coude. En effet, le format URDF ne permet pas l’utilisation d’une structure cinématique en graph, simplement en arbre.

Ce modèle est également utilisé avec l’outil de simulation physique Gazebo, (http://gazebosim.org/tutorials?tut=ros_overview) qui supporte les moteurs physiques (https://en.wikipedia.org/wiki/Physics_engine) ODE, Dart, Bullet et Simbody et utilise le moteur de rendu (https://en.wikipedia.org/wiki/Rendering_(computer_graphics)) OGRE. Il permet également d’intégrer au modèle des capteurs et des interfaces utilisateur. Cela en fait aujourd’hui l’un des simulateurs 3D de robotique les plus utilisés.

Nous avons donc créé sur Gazebo un monde virtuel dont nous avons paramétré la physique afin d’assurer une représentativité proche du robot réel. Avant d’envoyer une trajectoire sur le robot réel, vous pouvez donc vous assurer de son bon fonctionnement. De même, tous vos tests d’intégration continue de programmes peuvent être réalisés sans risquer d’endommager le robot.

## 6.4 Monitoring

Lors de la simulation comme lors du fonctionnement réel, il est possible de suivre sur l’outil rqt_gui (http://wiki.ros.org/rqt_gui) l’évolution de toutes les données échangées entre nos différents programmes, notamment les consignes de position et les valeurs renvoyées par les capteurs, mais aussi par exemple la fréquence de la boucle de contrôle.

## 6.5 Envoi de trajectoire sur POPI

Mises en garde :

- Dans sa version actuelle, le robot n’a pas de connaissance de son environnement immédiat. Il revient donc à l’utilisateur de s’assurer que le terrain sur lequel il évolue est similaire à celui utilisé pour générer la trajectoire de marche.
- Malgré une simulation représentative, il convient également de garder à l’esprit que le comportement du robot réel peut différer légèrement.
- Enfin, puisque sur Towr le robot démarre en position nominale, les trajectoires sont générées à partir de cette position : il faut donc prendre garde à le placer dans cette position avant d’envoyer une trajectoire. Pour cela, nous avons au préalable recours à une manette de Xbox branchée au PC utilisateur, paramétrée de sorte à permettre facilement l’envoi de la position nominale ou de la position de repos (décrit en 7.7.3).

La Figure 8 décrit le fonctionnement logiciel de POPI lors d’une marche réelle.

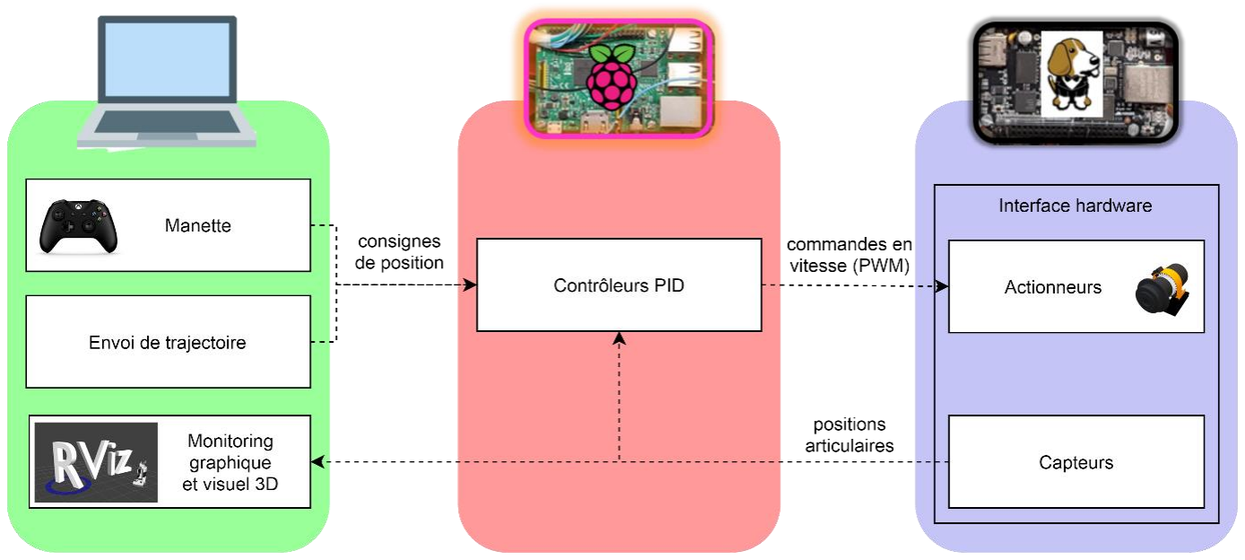
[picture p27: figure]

FI GU R E 8 : SC H EM A DE F ONC TION NEMEN T LOGIC IEL DE POPI

## 6.6 Arborescence des dossiers

FI GU R E 9 : AR BORESC EN CE D ES DOSSIER S

- Popi_code : Contient différents codes source C++ générés automatiquement.
- Popi_control : Contient la description des contrôleurs utilisés pour asservir les actionneurs ainsi que les routines permettant de faire lever le robot et de le mettre au repos.
- Popi_description : Contient le modèle virtuel du robot POPI ainsi qu’un fichier launch pour le visualiser sur Rviz.
- Popi_gazebo : Contient tous les fichiers de paramétrage de l’environnement de simulation ainsi qu’un fichier launch pour visualiser le robot sur Gazebo.
- Popi_robot : Contient les définitions des messages et des services utilisés pour communiquer l’état du robot et envoyer les commandes aux moteurs.
- Ifotp : Package permettant à Towr d’utiliser un solveur haute performance.
- Towr : Package contenant l’interface graphique permettant de générer des trajectoires pour robot à patte.
- Xpp : Package permettant la visualisation de trajectoire pour robot à patte sur Rviz. Il contient aussi des plug-ins affichant les zones et forces de contact au sol.
- Actionneurs : Contient les nœuds ROS qui communiquent avec les moteurs du robot.
- Capteurs : Contient les nœuds ROS qui communiquent avec les capteurs du robot.

## 7 Notice d’instruction

Cette notice d’instructions sera amenée à évoluer en même temps que le code source. Une simplification des procédures d’utilisation est à l’étude.

Note : Les mots de passe des cartes sont « ubuntu » pour la Raspberry Pi et « temppwd » pour les BeagleBone. Ils peuvent être modifiés par l’utilisateur si besoin.

## 7.1 Installation

Vous trouverez ci-dessous les étapes d’installation à réaliser sur le PC utilisateur afin d’utiliser les outils logiciels de POPI :

1. Disposer d’une session Ubuntu 18.04 (en machine virtuelle (https://doc.ubuntu-fr.org/virtualbox) ou en dual boot) (https://lecrabeinfo.net/installer-ubuntu-18-04-lts-dual-boot-windows-10.html)
2. Installer ROS melodic (http://wiki.ros.org/melodic/Installation/Ubuntu) full desktop (cette version contient nativement les outils tels que RViz, Gazebo et rqt)
3. [FACULTATIF] Installer le logiciel de traitement de texte Sublime text. (https://doc.ubuntu-fr.org/sublime-text) Pour cela, ouvrir un terminal (CTRL+ALT+T) et taper la commande suivante :
01. sudo apt-get install sublime-text

Un mot de passe vous sera demandé pour passer en super utilisateur (“sudo”), par défaut, c’est “ubuntu”, autrement il s’agit du mot de passe que vous avez défini lors de la création de votre session Ubuntu. Si vous êtes habitués à d’autres outils de traitement de texte, cette étape n’est pas nécessaire. Veillez, le cas échéant, à remplacer l’instruction « subl » des commandes par l’instruction appropriée (e.g. « nano »).

### 4. Installer les packages nécessaires :

01. sudo apt-get install ros-melodic-gazebo-ros ros-melodic-ros-control ros-melodic-gazebo-ros-control ros-melodic-gazebo-ros-pkgs ros-melodic-ros-controllers ros-melodic-robot-controllers ros-melodic-robot-state-publisher ros-melodic-joy git cmake libeigen3-dev coinor-libipopt-dev libncurses5-dev xterm
5. Nous utilisons la version de Gazebo 9.12.0. Il est possible que l’installation de ROS melodic ne vous fournisse que la version 9.0.0. Vous pouvez le vérifier en tapant la commande :
01. gazebo -v

Si vous n’avez pas la version 9.12.0, procédez comme suit :
01. sudo subl /etc/apt/sources.list.d/gazebo-stable.list
Dans | le fichier texte qui | vient de s’ouvrir, vérifiez que | l’adresse est | bien | : | deb
http://packages.osrfoundation.org/gazebo/ubuntu-stable bionic main, remplacez-la si ce n’est pas le cas.

### 6. Enfin, mettez à jour l’ensemble de vos sources :

01.
02.

sudo apt-get update
sudo apt-get upgrade

### 7. Récupérer puis compiler le dossier popi_ros présent sur le GitHub du projet :

01.
02.
03.

mkdir –p ~/catkin_ws/src
cd ~/catkin_ws/src
git clone https://github.com/popi-mkx3/popi_ros.git

04.
05.

cd ~/catkin_ws
catkin_make_isolated
8. Ouvrez votre fichier .bashrc (les instructions qu’il contient seront effectuées automatiquement à chaque ouverture de terminal) :
01. sudo subl ~/.bashrc

Ajoutez, à la fin de ce fichier, les quatre lignes suivantes, puis sauvegardez le fichier :

source /opt/ros/melodic/setup.bash
source ~/catkin_ws/devel_isolated/setup.bash
#export ROS_IP=192.168.7.4

#export ROS_MASTER_URI=http://192.168.7.1:11311

Important : pour les parties 7.3 à 7.6 , il n’est pas nécessaire de disposer de la plateforme POPI ni d’y être branché. Toutes les instructions s’effectuent sur le PC utilisateur. Assurez-vous que les deux dernières lignes dans votre fichier .bashrc sont commentées (présence du #), sans quoi les instructions de ces trois parties ne fonctionneront pas.
À l’inverse, il faudra penser à décommenter ces deux lignes (enlever les #) lors de l’utilisation de la plateforme POPI (partie 7.70).

## 7.2 Raccordement / alimentation

Pour utiliser le robot il faut dans un premier temps le raccorder à la platine d’alimentation. Avant de commencer, assurez-vous que la platine soit branchée, et que tous les interrupteurs soient placés sur off : l’interrupteur différentiel, les deux disjoncteurs et le commutateur 24V (voir Figure 5).

Branchez ensuite le câble RJ45 sur le port Ethernet de la Raspberry. Installez le carter en plexiglass et fixez-le avec ses vis. Branchez les trois câbles restant sur les bons connecteurs et attachez les mousquetons comme présenté sur la Figure 10.

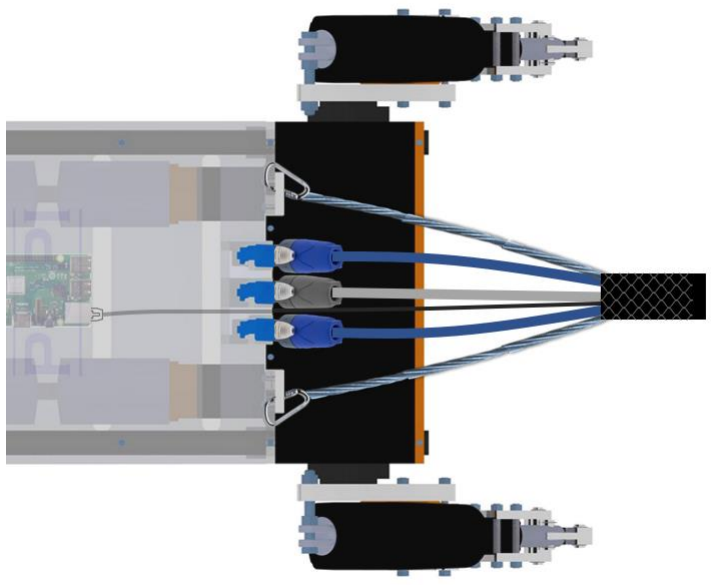
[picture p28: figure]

FI GU R E 10 : BRAN CH EM ENT D E L'OM BILIC.

Une fois tous les câbles correctement branchés, positionnez sur ON les interrupteurs suivants : interrupteur différentiel, disjoncteur 230V, disjoncteur 24V. Connectez le PC utilisateur de l’autre côté de l’ombilic au niveau de la platine d’alimentation. Essayez de ping les adresses IP des trois cartes jusqu’à ce que la communication soit opérationnelle. Une fois que les cartes ont démarrée correctement, la plateforme POPI est prête à l’emploi.

Suivre toutefois les précautions suivantes :

- Avant d’activer le 24V, veiller qu’aucune commande ne soit envoyé sur les actionneurs
- Ne pas activer le 24V si le ping des cartes Raspberry et BBB ne fonctionne pas.
- Le robot est équipé de deux sécurités majeures en cas d’envoi d’une commande trop importante : les alimentations se mettront en défaut durant 3 secondes lors d’un appel de courant trop important, les cartes contrôleurs possèdent des condensateurs capables d’absorber d’importants appels de courants.
- Si une alimentation se met en défaut, appuyer rapidement sur l’arrêt d’urgence ou positionner le commutateur 24V sur OFF et analyser les commandes envoyées aux actionneurs avant de le réactiver.
- Lorsque le commutateur 24V est positionné sur OFF, attendre 45s que les condensateurs des alimentations se déchargent avant toute intervention sur le robot.
- Si aucun des voyants de la platine ne s’allume, vérifier que le bouton d’arrêt d’urgence ne soit pas enclenché.

## 7.3 Génération de trajectoires

Pensez à vérifier votre fichier bashrc comme indiqué en fin de partie 7.1.

7.3.1 Utilisation de Towr

### 1. Sur le PC utilisateur, lancez l’interface Towr :

01. roslaunch towr_ros towr_ros_popi.launch

Cette commande permet l’ouverture de l’interface utilisateur de Towr (Figure 11) et de Rviz (Figure 12).

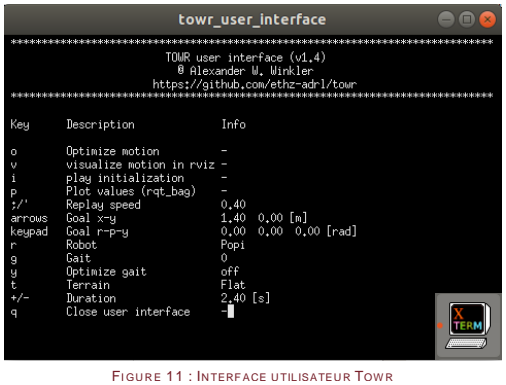
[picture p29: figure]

FI GU R E 11 : IN TERF ACE U TILISATEU R TOW R

FI GU R E 12 : IN TERF ACE RVI Z
Pour afficher le visuel 3D sur RViz, cochez la case comme indiqué en Figure 12 (1), sélectionnez l’interface utilisateur de Towr et cliquez sur « i » pour lancer la séquence d’initialisation.

L’interface utilisateur de Towr est très intuitive et facile à prendre en main, les touches sont indiquées dans la colonne key.

2. Déplacez l’objectif à atteindre avec POPI (représenté par le trièdre en 2) (flèches directionnelles et pavé numérique).
3. Choisissez le terrain désiré (« t »).
4. Choisissez la démarche à adopter, les seules ayant été testées en réel sont la 0 et la 1 (« g ») :
- 0 : démarche statique : pattes gauches puis droites
- 1 : démarche dynamique : les pattes diagonales bougent ensemble
- 2 : démarche dynamique : pattes gauches puis droites
- 3 : démarche dynamique : pattes avant arrière
- 4 : démarche statique : pattes avant puis arrière

### 5. Lancez le calcul de la trajectoire (« o »)

6. Vous pouvez par la suite revoir le mouvement du robot en appuyant sur « v » (en appuyant de nouveau sur « o », un nouveau calcul serait effectué).
7. Ajustez avec précaution la vitesse du mouvement avec les touches « ; » et « ‘ ». La vitesse de visualisation correspondra également à la vitesse à laquelle vos commandes seront envoyées sur le robot réel !

7.3.2 Enregistrement des commandes en rosbag
1. Une fois satisfait de la trajectoire que vous avez créée, il vous faut l’enregistrer. Pour ce faire, ouvrez rqt_bag :
| 01. | | cd ~/catkin_ws/src/popi_ros/popi/popi_robot/trajectories/bags
02. | | rosrun rqt_bag rqt_bag

2. Pour démarrer l’enregistrement, cliquez sur le cercle rouge situé en haut à gauche de la fenêtre. La nouvelle fenêtre en Figure 13 apparaît. Comme sur l’image, sélectionnez les 12 topics /popi/…/command qu’on souhaite surveiller puis appuyez sur Record. Choisissez un nom pour votre fichier (e.g. « ma_marche ») et cliquez sur Save.

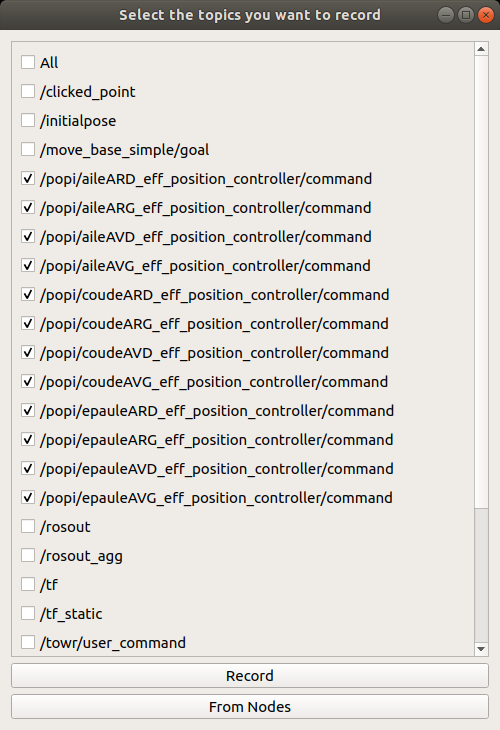
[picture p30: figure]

3. Vous pouvez à présent revenir sur l’interface utilisateur Towr et taper « v ». Sur rqt_bag s’affichent les trames enregistrées comme sur la Figure 14.

FI GU R E 13 : SELECTI ON D ES TOPIC S SUR RQT_BAG

4. Lorsque votre trajectoire est terminée, vous pouvez à nouveau cliquer sur le bouton rouge en haut à gauche pour mettre fin à l’enregistrement.

7.3.3 Modifier les commandes sur un tableur
1. Afin de modifier les commandes sur un tableur (e.g. Excel), il faut convertir le fichier rosbag que nous avons créé en format csv. On ne peut le faire qu’un topic à la fois pour le moment, et on va donc commencer par créer 12 fichiers csv différents.

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
cd ~/catkin_ws/src/popi_ros/popi/popi_robot/trajectories/bags rostopic echo -b ma_marche.bag -p /popi/aileAVD_eff_position_controller/command > ../csv/aileAVD.csv rostopic echo -b ma_marche.bag -p /popi/aileAVG_eff_position_controller/command > ../csv/aileAVG.csv rostopic echo -b ma_marche.bag -p /popi/aileARD_eff_position_controller/command > ../csv/aileARD.csv rostopic echo -b ma_marche.bag -p /popi/aileARG_eff_position_controller/command > ../csv/aileARG.csv rostopic echo -b ma_marche.bag -p /popi/epauleAVD_eff_position_controller/command > ../csv/epauleAVD.csv rostopic echo -b ma_marche.bag -p /popi/epauleAVG_eff_position_controller/command > ../csv/epauleAVG.csv rostopic echo -b ma_marche.bag -p /popi/epauleARD_eff_position_controller/command > ../csv/epauleARD.csv rostopic echo -b ma_marche.bag -p /popi/epauleARG_eff_position_controller/command > ../csv/epauleARG.csv rostopic echo -b ma_marche.bag -p /popi/coudeAVD_eff_position_controller/command > ../csv/coudeAVD.csv rostopic echo -b ma_marche.bag -p /popi/coudeAVG_eff_position_controller/command > ../csv/coudeAVG.csv rostopic echo -b ma_marche.bag -p /popi/coudeARD_eff_position_controller/command > ../csv/coudeARD.csv rostopic echo -b ma_marche.bag -p /popi/coudeARG_eff_position_controller/command > ../csv/coudeARG.csv

FI GU R E 14 : FEN ETRE R QT_BAG PEN DANT L'EN R EGI STREM ENT

2. Une fois les 12 fichiers csv, vous pouvez les importer sur votre tableur et les assembler (ils se trouvent dans le dossier ~/catkin_ws/src/popi_ros/popi/popi_robot/trajectories/csv).
3. Les timestamps utilisés par rqt_bag sont particuliers : afin d’obtenir votre temps en secondes écoulées depuis le début de l’enregistrement, il faut effectuer le calcul suivant :

t =

%time
10⁹

− X

Où X est tel qu’indiqué en Figure 14 sur votre rosbag.

4. Une fois vos modifications effectuées sur le tableur, il faut effectuer la conversion inverse. Pour ce faire, il faut d’abord organiser votre tableau ainsi : en première ligne, les titres de colonnes doivent être, dans l’ordre : %time, aileAVD, aileAVG, aileARD, aileARG, epauleAVD, epauleAVG, epauleARD, epauleARG, coudeAVD, coudeAVG, coudeARD, coudeARG.

### 5. Une fois le modèle respecté, enregistrez votre fichier, par exemple sous le nom

« ma_marche_modifiee.csv ». Vérifiez en ouvrant ce fichier avec un éditeur de texte (e.g. Notepad++) que votre tableur a créé un format csv identique à ceux des fichiers initiaux (utilisant des « , » et pas des « ; », etc.)

### 6. Enfin, ouvrez un terminal et tapez les commandes suivantes :

01. | | cd ~/catkin_ws/src/popi_ros/popi/popi_robot/trajectories/csv
02. | ./csv_to_rosbag.py ma_marche_modifiee mv ma_marche_modifiee.bag ../bags/
03.

## 7.4 Utilisation de la manette

Comme expliqué dans la partie 6.5, il est nécessaire de placer POPI en position nominale avant de pouvoir utiliser une trajectoire. Cela vaut pour la simulation comme pour l’envoi sur le robot. Pour ce faire, nous avons développé un programme se reposant sur une manette, qui offre également d’autres possibilités. La configuration de la manette se trouve en Figure 15.

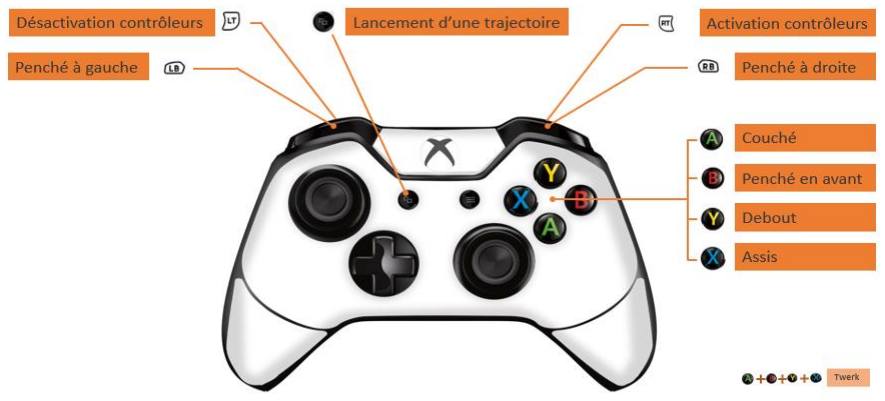
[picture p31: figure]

En cas de problème d’utilisation de la manette, vous pourrez obtenir de plus amples renseignements sur la page du package teleop_joy (http://wiki.ros.org/joy/Tutorials/WritingTeleopNode) que nous utilisons.

FI GU R E 15 : CONFI GURATI ON D E LA M AN ETTE

## 7.5 Simulation

Pensez à vérifier votre fichier bashrc comme indiqué en fin de partie 7.1.

Maintenant, il vous est possible de vérifier ce que donne la trajectoire créée sur Gazebo.

1. Ouvrez un terminal et entrez la commande suivante :
01. roslaunch popi_robot popi_simu.launch
2. Utilisez la touche | de la manette pour mettre POPI en position nominale.
3. Dans un nouveau terminal :

01.
02.

cd ~/catkin_ws/src/popi_ros/popi/popi_robot/trajectories/bags rosbag play ma_marche.bag

## 7.6 Monitoring

Pour assurer le monitoring des données échangées entre les programmes, ouvrir un terminal et taper la commande :

01. rosrun rqt_gui rqt_gui

Une fenêtre qui contient les Figure 16 et Figure 17 s’ouvre :

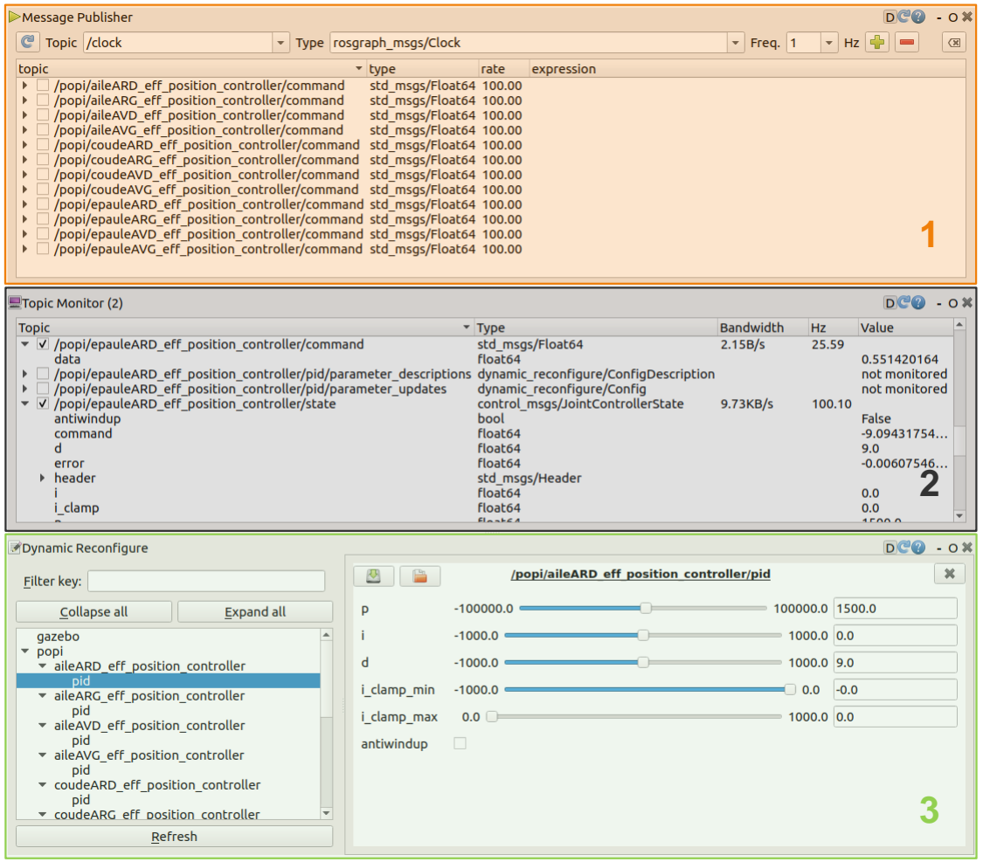
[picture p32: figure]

FI GU R E 16 : IN TERF ACE R QT_GU I – MESSAGE PUBLISH ER (1), TOPI C M ONITOR (2) ET D YNAM IC R ECON FIGU RE (3)

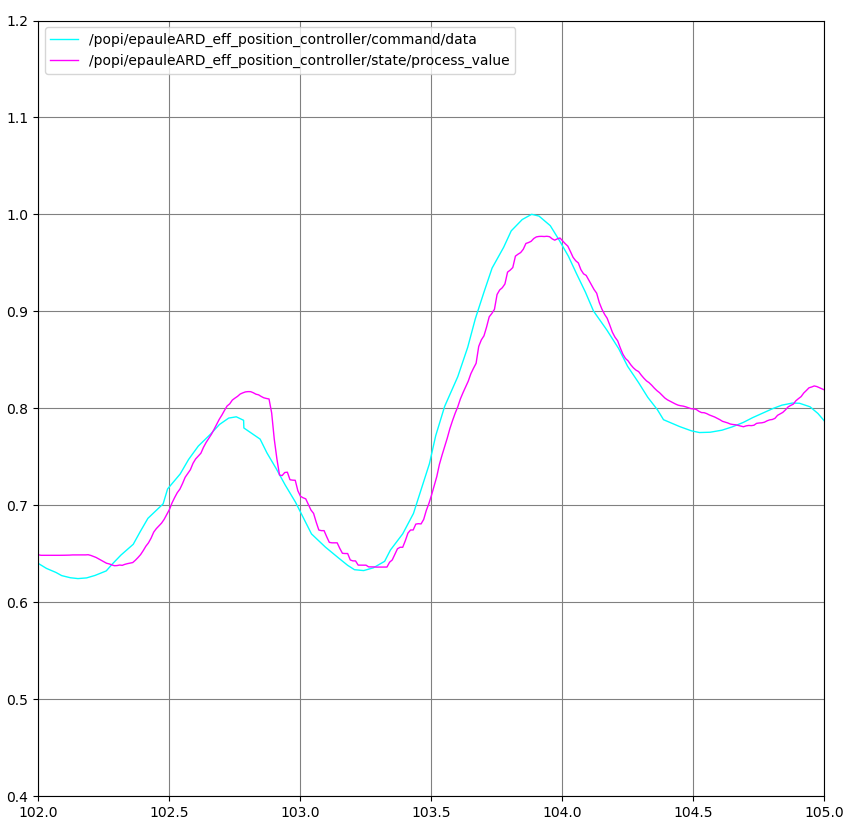
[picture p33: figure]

Explication des outils :

1. Message publisher : cet outil permet d’envoyer depuis l’interface un message, par exemple d’écrire la commande « 1.0 » en radian sur l’épaule arrière droite. On le retrouve dans Plugins/Topics
2. Topic monitor : cet outil permet de sélectionner les topics que l’on veut surveiller en « temps réel ». Il suffit de les cocher. On le retrouve également dans Plugins/Topics.
3. Dynamic Reconfigure : il autorise le changement dynamique des valeurs de notre système, dont notamment les valeurs des coefficients des PID. Il se trouve dans Plugins/Configuration.
4. Enfin, l’outil plot permet comme le topic monitor de surveiller des topics, mais avec un tracé graphique. On peut glisser/déposer depuis le topic monitor dans le plot les topics voulus.

Rqt_gui est un outil aux multiples possibilités. Le plus efficace est de le prendre en mains pour apprendre à s’en servir.

FI GU R E 17 : IN TERF ACE R QT_PLOT

## 7.7 Envoi de trajectoire sur POPI

7.7.1 Mode opératoire de manutention
Si le robot est en position de repos, il peut être déplacé directement sur son socle à roulette. S’il n’est pas en mode de repos, le robot POPI doit être déplacé par deux utilisateurs avec les poignées fournies, en les positionnant comme en Figure 18.

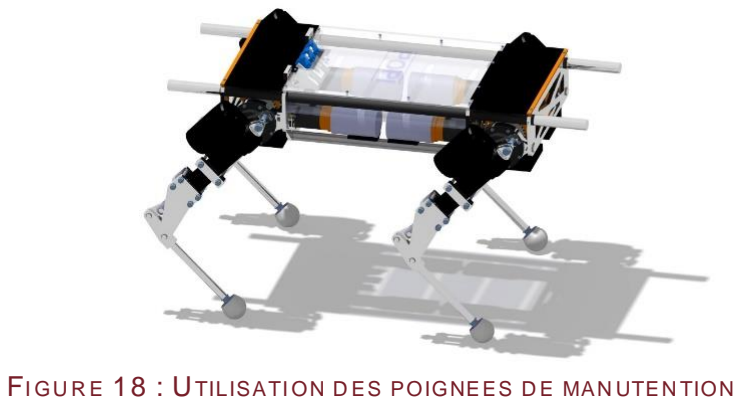
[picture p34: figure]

7.7.2 Première connexion

Lors de la première connexion du PC utilisateur au câble Ethernet de l’ombilic, vous devrez effectuer certaines opérations afin de l’intégrer correctement au réseau de POPI.

PARAMETRAGE DE L’ADRESSE IP

Dans un premier temps il faut donner au PC l’adresse IP 192.168.7.4 :

1. Ouvrez les paramètres réseau et éditez la connexion filaire.

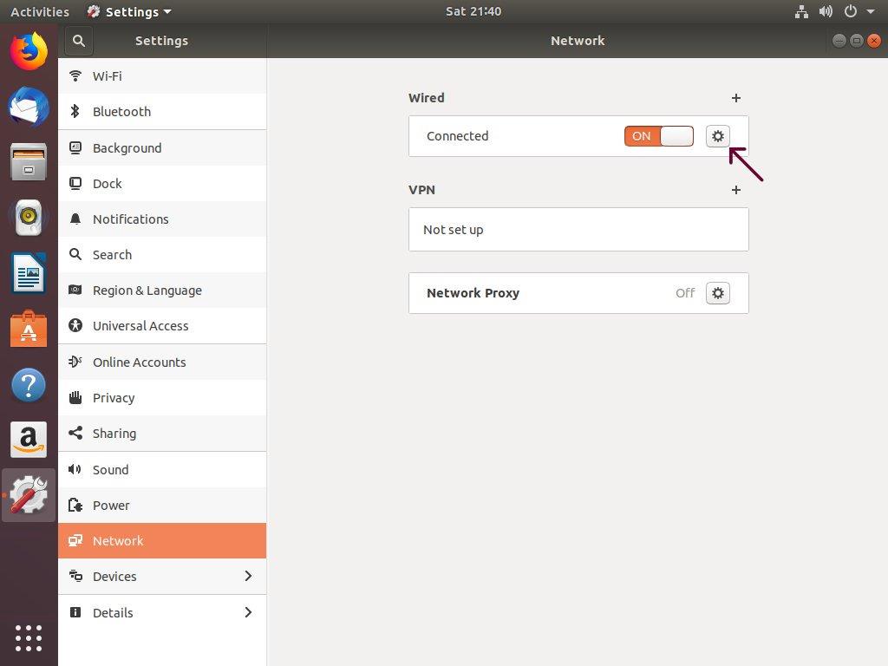
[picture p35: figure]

FI GU R E 19 : PAGE DE PAR AMETR AGE RESEAU

FI GU R E 18 : UTILISATI ON D ES POIGNEES D E MAN UTEN TION

### 2. Dans l’onglet IPV4, sélectionnez la méthode manuelle et paramétrez la partie adresse

comme indiqué sur l’image ci-dessous.

FI GU R E 20 : PAGE DE PAR AMETR AGE DE LA C ONN EXI ON F ILAIRE

3. Avant de valider, vérifiez dans l’onglet détails que les cases suivantes sont bien cochées.

FI GU R E 21 : ON GLET D ETAI L DE LA PAGE D E PARAM ETRAGES D E LA CON NEXION F ILAIR E

AJOUT DES NOMS D’HOTES

Pour ne pas avoir à saisir à chaque fois les adresses IP, on utilise des noms d’hôtes qui permettent de se substituer à celles-ci.

### 1. Ouvrez le fichier /etc/hosts :

01. sudo subl /etc/hosts
2. Ajoutez les lignes suivantes à la fin du fichier.

01.
02.
03.

192.168.7.1 popi-raspi
192.168.7.2 beagle-droite
192.168.7.3 beagle-gauche

ROS_IP ET ROS_MASTER_URI

1. Ouvrez le fichier .bashrc :
01. sudo subl ~/.bashrc

2. Décommentez les deux lignes suivantes (supprimer le #), puis sauvegardez le fichier :

#export ROS_IP=192.168.7.4

#export ROS_MASTER_URI=http://192.168.7.1:11311

PARAMETRAGE DES CONNEXIONS SSH

### 1. Pour commencer, il faut ouvrir un serveur SSH sur le PC :

01.
02.

sudo apt-get update
sudo apt-get install openssh-server

Le serveur SSH s’active automatiquement.

Il faut maintenant établir une première connexion SSH aller et retour avec toutes les cartes :

### 2. Établir la connexion depuis votre PC vers la Raspberry PI :

01. ssh ubuntu@popi-raspi -oHostKeyAlgorithms=’ssh-rsa’

Le mot de passe de la raspberry est : ubuntu

### 3. Établir la connexion depuis la Raspberry vers votre PC :

01. ssh user@pc -oHostKeyAlgorithms=’ssh-rsa’

Remplacer « user » par votre nom d’utilisateur. Le mot de passe à saisir est celui de votre PC.

### 4. Établir la connexion depuis votre PC vers la BeagleBoneBlack droite :

01. ssh debian@beagle-droite -oHostKeyAlgorithms=’ssh-rsa’

Le mot de passe des beaglebone est : temppwd

### 5. Établir la connexion depuis la BeagleBoneBlack droite vers votre PC :

01. ssh user@pc -oHostKeyAlgorithms=’ssh-rsa’

Remplacer « user » par votre nom d’utilisateur. Le mot de passe à saisir est celui de votre PC.

### 6. Établir la connexion depuis votre PC vers la BeagleBoneBlack gauche :

01. ssh debian@beagle-gauche -oHostKeyAlgorithms=’ssh-rsa’

Le mot de passe est : temppwd

### 7. Établir la connexion depuis la BeagleBoneBlack gauche vers votre PC :

01. ssh user@pc -oHostKeyAlgorithms=’ssh-rsa’

Remplacer « user » par votre nom d’utilisateur. Le mot de passe à saisir est celui de votre PC.

7.7.3 Utilisation des trajectoires
Merci de reprendre connaissance des mises en garde données en partie 6.5.

### 1. Commencez par placer manuellement les épaules à leur « zéro » initial, autrement dit à

l’horizontale. L’utilisation d’un niveau à bulles est recommandée. Cette étape n’est pas facultative : lors du lancement de la commande suivante, le programme enregistre la position actuelle des épaules comme leur « zéro ». Si elles n’y sont pas réellement, toutes les commandes envoyées seront interprétées avec le décalage de l’initialisation !
Dans l’idéal, POPI devrait être dans une position proche de celle en Figure 22.

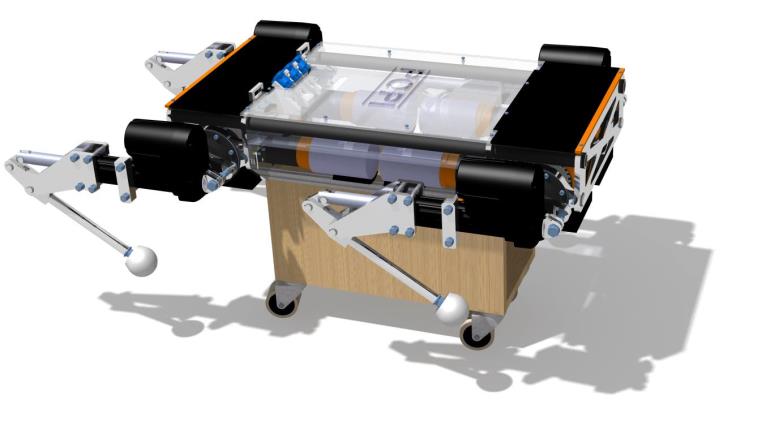
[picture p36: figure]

FI GU R E 22 : POPI EN POSI TION REPOS

### 2. Ouvrir un terminal et entrez la commande suivante :

01. roslaunch popi_robot beagles.launch

### 3. Dans un nouveau terminal, entrez la commande :

01. ssh ubuntu@192.168.7.1

Une fois connecté sur la Raspberry Pi (mot de passe ubuntu), tapez :

01. roslaunch popi_robot hw_interface.launch

### 4. Dans un troisième terminal:

01. roslaunch popi_robot popi_reel.launch

### 5. Utilisez la touche de la manette pour vous assurer que les commandes envoyées soient

celles de la position de repos.

6. Allumez le 24V en tournant le commutateur sur la platine d’alimentation (voir Figure 5).
7. Utilisez la touche | de la manette pour démarrer les contrôleurs. Vous pouvez vérifier
dans l’onglet Dynamic Reconfigure de rqt_gui que les valeurs des coefficients « P » des contrôleurs ne sont plus à 0.
Lors de cette étape, s’il y avait un écart entre la position actuelle de POPI et les dernières commandes envoyées au robot, les actionneurs vont bouger. Pour ne pas entraîner de mouvements brusques des actionneurs, nous privilégions des commandes de type rampes. Cet écart peut au contraire résulter en échelon important ! Soyez donc vigilants.

8. Utilisez la touche de la manette pour mettre POPI en position nominale, comme en Figure 23.
9. Retirez le socle.

### 10. Dans un quatrième terminal, envoyez la trajectoire voulue :

01. | | cd ~/catkin_ws/src/popi_ros/popi/popi_robot/trajectories/bags
02. | rosbag play ma_marche.bag

En cas de problème, vous pouvez immédiatement mettre fin à une marche en appuyant sur la touche

de la manette. Cela a pour effet de remettre tous les coefficients « P » des contrôleurs à 0, ce qui implique que les moteurs ne reçoivent plus aucune commande.

Attention, si le robot n’est pas dans une position équilibrée, cette action présente un risque de chute ! Dans le cas contraire, POPI tient mécaniquement sur ses quatre pattes sans avoir besoin de lui envoyer des commandes.

11. Les trajectoires générées par Towr ne finissent généralement pas en position nominale. Pensez à repositionner POPI (voir étape 8) pour assurer son bon équilibre.
Lorsque la trajectoire envoyée est terminée, vous pouvez immédiatement en envoyer une autre sans refaire l’ensemble des étapes. Gardez néanmoins à l’esprit qu’une utilisation intensive des vérins peut provoquer leur détérioration du fait de leur duty cycle limité (voir Tableau 4).

7.7.4 Trajectoires mises à disposition
Cinq trajectoires sont mises à disposition par l’équipe. Pour y accéder, vous pouvez vous rendre dans le dossier ~/catkin_ws/src/popi_ros/popi/popi_robot/trajectories/bags. Ces trajectoires sont les suivantes :
- short_static_walking.bag : POPI avance en marche statique sur sol plat, sur une distance de 80cm.
- short_dynamic_walking.bag : POPI avance en marche dynamique sur sol plat, sur une distance de 80cm.
- long_dynamic_walking.bag : POPI avance en marche statique sur sol plat, sur une distance de 4m.
- step_20cm.bag : POPI franchit, en marche statique, une marche de 20cm de haut.
- pit_30cm.bag : POPI franchit, en marche statique, une fosse de 30cm de large.

Il est possible d’obtenir un aperçu vidéo de la configuration des terrains et des trajectoires réalisées sur le GitHub (https://github.com/popi-mkx3/popi_ros) du projet.

Les deux dernières trajectoires n’ont jamais été testées en réalité. L’équipe POPI se dégage de toute responsabilité en cas de dégâts survenus suite à l’utilisation d’une de c es trajectoires ou d’une autre trajectoire qui n’a pas été validée par ses soins.

FI GU R E 23 : POPI EN POSI TION NOM INALE

7.7.5 Mise en position repos
Pour pouvoir mettre POPI en position repos, il faut que le robot soit alimenté et qu’il soit en l’état de recevoir des commandes. Lorsque vous n’utilisez pas POPI, merci de le replacer en position de repos sur son socle :
1. Positionnez le socle à roulette en-dessous du robot comme sur la Figure 24.
2. Utilisez la touche de la manette pour mettre POPI en position de repos sur son socle. Il est conseillé que 2 manutentionnaires se munissent des poignées pour accompagner le mouvement du robot.
3. Une fois le robot sur son socle, vous pouvez fermer les processus en cours dans vos différents terminaux (CTRL+C) dans l’ordre inverse de celui dans lequel vous les avez ouverts. Enfin, vous pouvez couper l’alimentation.

## 8 Sécurité

## 8.1 Prescription générale de sécurité

Cette notice d’instructions ne prend en compte que les comportements raisonnablement prévisibles. Le produit POPI est conçu et réalisé en considérant toujours la sécurité de l’opérateur, toute utilisation autre que celle indiquée sur la présente notice d’instructions peut constituer un danger.

Suivre les précautions suivantes :

- Avant toute utilisation, vérifier que la machine est montée correctement dans son ensemble.
- Conserver une zone de travail propre et ordonnée.
- Positionner la machine dans une zone de travail suffisamment éclairée.
- Ne pas endommager le câble d’alimentation électrique.
- Ne jamais tirer sur le câble d’alimentation électrique pour le retirer de la prise de courant.
- Maintenir le câble d’alimentation électrique éloigné des sources de chaleur, des parties grasses et/ou des bords tranchants.
- Protéger le câble d’alimentation électrique contre l’humidité et tous risques éventuels de dégradations.
- Vérifier périodiquement le câble d’alimentation électrique et s’il est endommagé, le faire réparer par un réparateur agréé.
- Les protections mécaniques et/ou électriques ne doivent pas être enlevées ou shuntées.
- Aucune modification et/ou reconversion ne doit être effectuée.

FI GU R E 24 : POSITI ONN EM ENT D U SOCLE

- Seul le personnel compétent et qualifié est autorisé à réparer ou remplacer les pièces endommagées.
- Ne pas toucher le robot en mouvement.
- Pour toute opération présentant des risques de pincement, happement, enroulement, écrasement, arrêter la machine et porter des gants de protection.
- Déconnecter l’alimentation électrique pour toute opération plus importante (maintenance, entretien …).
- Ne pas nettoyer le robot ou le système embarqué lorsqu’ils sont en mouvement.
- Ne pas laver la machine avec un jet d’eau sous pression, car risque de faire pénétrer celle-ci dans la partie électrique.
- Ne pas utiliser de solvant ou de détergents agressifs.
- Couper l’alimentation et vérifier que les parties mobiles sont bloquées, lors du déplacement.
- Ne pas utiliser la machine sans une formation suffisante.

## 8.2 Transport

Le transport et le déplacement du robot, lorsqu’il est à l’arrêt, doivent se faire sur son support à roulette ; le robot doit être en position de repos, les vérins doivent être sortis de façon à ce que l’angle formé par les pattes fasse 15°.

Si le robot n’est pas positionné sur son socle, le robot POPI peut être déplacé grâce aux poignées fournies.

Le robot pèse 70kg, il ne peut pas être transporté par une personne seule. Il faut au minimum 2 personnes pour le déplacer.

## 8.3 Installation / Désinstallation

Lors de l’installation du robot dans son environnement, commencer par vérifier l’état général du produit. Lors de la réception, le produit POPI est sur son socle de repos. Le produit POPI doit être démarré dans cette position, et remis dans cette position à chaque fin d’utilisation.

Pour cela, il faut que le robot POPI soit relié à sa platine d’alimentation.

Les opérations électriques doivent être effectuées par un personnel qualifié et habilité aux travaux électriques basse tension. S’assurer que la tension d’alimentation de l’installation correspond à celle nécessaire par la platine d’alimentation. Contrôler que l’installation électrique sur laquelle le robot POPI est branché est bien reliée à la terre conformément aux normes de sécurité en vigueur.

Connecter les câbles d’alimentation du produit POPI au tableau d’alimentation

L’usage de l’appareil avec un câble endommagé est rigoureusement interdit. Vérifier régulièrement l’état des câbles d’alimentation.

## 8.4 Maintenance

Avant toute opération de maintenance ou d’entretien, déconnecter l’alimentation électrique. Débrancher l’ombilic et attendre 45 secondes afin de s’assurer que le produit POPI est complètement hors tension. Désactiver toute autre source d´énergie connectée au robot et à la platine d’alimentation. Prendre les précautions nécessaires pour empêcher que d’autres personnes activent le système pendant la période de réparation.

Vérifier la connexion de terre avant de remettre le système sous tension.

N’utilisez jamais d’air comprimé pour nettoyer le robot, car cela pourrait endommager les composants électriques.

L’acquisition de deux pattes supplémentaires du robot quadrupède POPI est vivement conseillée afin de pallier rapidement les problèmes mécaniques pouvant survenir.

L’acquisition d’un double des cartes électroniques du robot quadrupède POPI est vivement conseillée, il n’est pas garanti que les cartes électroniques soient toujours produites à l’avenir, des versions supérieures pourront être installées sous réserve de leurs intégrations.

8.4.1 Instructions de maintenance préventive
Le prototype de robot quadrupède POPI à une durée de fonctionnement de 500h. Afin d’atteindre et de prolonger cette limite, veuillez effectuer les actions de maintenance préventive ci-dessous :

Note : Certaines actions ci-dessous nécessitent le démontage/montage du robot. Pour se faire, se référer à la notice de montage/démontage.

Toutes les 5h de fonctionnement :

Libellé | Fréquence | Détail
Vérification visuelle | Toute les 5h de fonctionnement | Vérification visuelle du robot par un utilisateur du robot.

Toutes les 50h de fonctionnement :

Libellé | Fréquence | Détail
Graissage | Toutes les 50h de fonctionnement | Démontage intégral du robot et remontage avec graissage des liaisons avec un produit adapté aux métaux (ex. : WD40).
Serrage | Toutes les 50h de fonctionnement | Vérification des couples de serrages à la clef dynamométrique. Resserrage si nécessaire.
Électronique 1 | Toutes les 50h de fonctionnement | Vérification des tensions des cartes électroniques et du bruit.

Toutes les 500h de fonctionnement :

Libellé | Fréquence | Détail
Électronique 2 | Tous les 500h de fonctionnement | Changement de toutes les cartes électroniques.
Vernissage | Tous les 500h de fonctionnement | Démontage intégral du robot. Vernissage de toutes les pièces métalliques avec un vernis incolore mat (ou équivalent).
Mécanique | Tous les 500h de fonctionnement | Changement des axes de liaisons pivots et changement des clavettes moteurs.
8.4.2 | Instructions de maintenance corrective

# INSTRUCTION DE MAINTENANCE

Maintenance corrective des pièces mécaniques :

Dans le cas d’un défaut mécanique sur l’une des pièces. Veuillez faire usiner la pièce aux côtes spécifiées dans les plans mécaniques. Pour les pièces imprimées en 3D, veuillez les réimprimer avec une imprimante frittage (ou équivalent).

Maintenance corrective de l’électronique :

Dans le cas d’un défaut sur l’une des cartes électroniques de puissance ou de commande, veuillez la remplacer.

Si besoin, les images des cartes SD des BeagleBoneBlack et de la Rasp berry PI sont disponibles sur le GitHub (https://github.com/popi-mkx3/popi_ros) du projet et peuvent être flashées sur une nouvelle carte (prévoir au moins 16 Go) à l’aide par exemple du logiciel BalenaEtcher. (https://www.minimachines.net/tutos/etcher-flasher-image-usb-50144)

Lors du remplacement de la Raspberry PI, une manipulation réseau est nécessaire pour assurer le bon fonctionnement du pont réseau br0. En effet, ce sont les adresses physiques des ports qui sont utilisées pour identifier les interfaces à relier en pont, et ces adresses physiques changent avec la carte. Pour ajouter les nouvelles adresses dans le pont, il faut connecter un écran sur le port HDMI de la Raspberry PI et redémarrer la carte. Dans la partie droite de la barre des tâches cliquer sur l’icône réseau puis sur « connections information ». Cette fenêtre permet d’identifier l’adresse physique des ports connectés aux adresses IP 192.168.7.2, 192.168.7.3 et 192.168.7.4. Il faut ensuite à nouveau cliquer sur l’icône réseau et ouvrir la fenêtre « edit connections » puis double cliquer sur le pont br0 (tout en bas) afin de l’éditer. Il faut alors s’assurer que les interfaces identifiées précédemment apparaissent bien sous le pont.

Si ce n’est pas le cas il faut les ajouter de la manière suivante :

1. Cliquer sur « add » pour ajouter une connexion.

FI GU RE 25 : AJOUT D'UNE CONNEXION PAR PONT.

2. Sélectionner le type de connexion « Ethernet ».
3. Sélectionner l’interface à ajouter dans le pont.

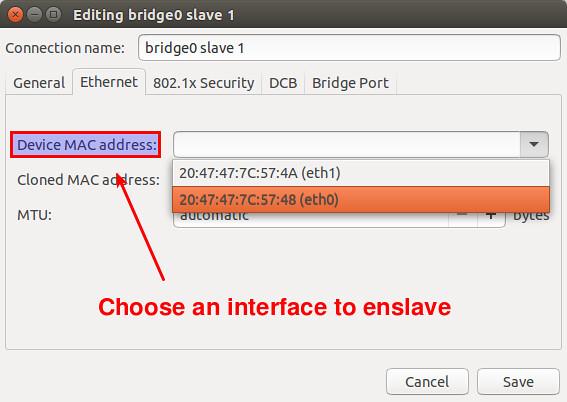
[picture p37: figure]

FI GU RE 26 : SELECTION DE L'INTERFACE A ASSERVIR
4. Sélectionner l’onglet « general » et vérifier que les cases suivantes sont bien cochées puis cliquer sur « save ».

FI GU RE 27 : VERIFICATION DE PARAMETRES RESEAUX

Afin de vérifier que les connexions sont rétablies, un test de ping pourra être effectué depuis le PC vers la Raspberry PI puis vers les deux BeagleBoneBlack.

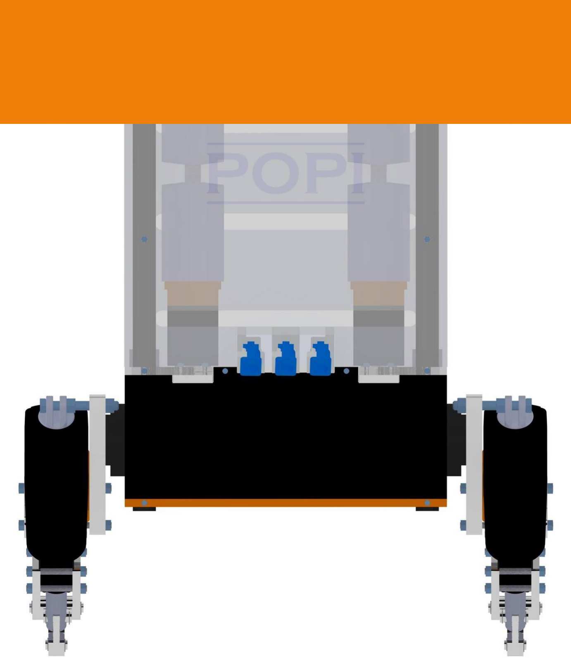
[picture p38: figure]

# POPI

# Annexe 1 : Plans de montage électronique

Qté | Nom | N°
1 2 | Partie intelligence Raspberry pi 3B+ BeagleBoneBlack | 1 2
4 8 2 2 1 1 2 1 2 | Partie distributions Contrôleur moteur Cytron 24V 20A Contrôleur moteur Cytron 24V 13A Bornier de distribution 1.8V, 5V et Ground Bornier 24V Bornier 230V HUB USB 60W Alimentation 24V 40A 1000W Boitier arrêt d’urgence Disjoncteur de type courbe C | 3 4 5 6 7 8 9 10 11
4 4 4 4 2 1 | Partie capteurs Potentiomètres 1kΩ Carte capteurs courants Capteur de positions vérin Carte roues codeuses Quadrature encoder counter Centrale inertielle | 12 13 14 15 16 17
4 4 4 | Partie actionneurs Moteurs MY1016 480W Moteurs MR997 300W Vérins MA2 300W | 18 19 20 21

TABLEAU 8 : NOM EN CLATU RE D ES COM POSAN TS ELECTR ON IQUE

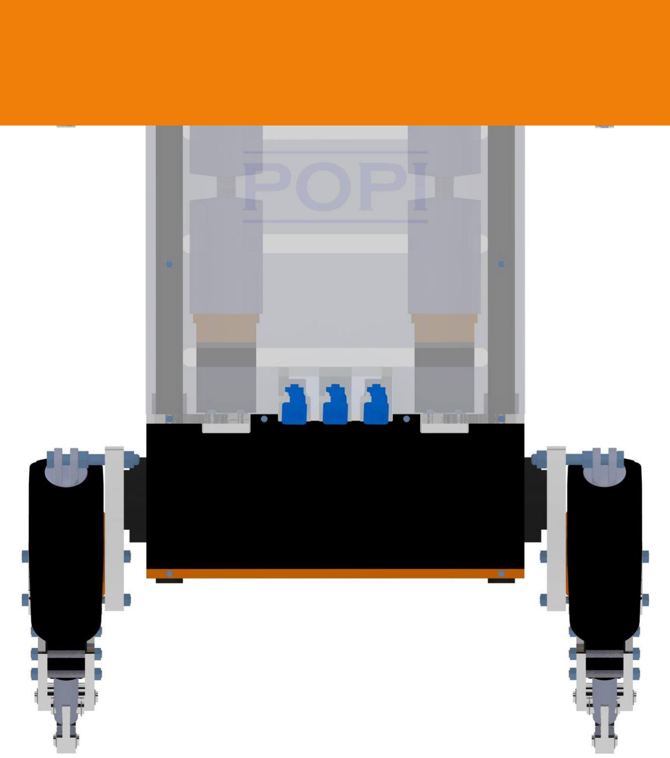
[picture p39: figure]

# POPI

# Annexe 2 : Notice de montage mécanique

# POPI

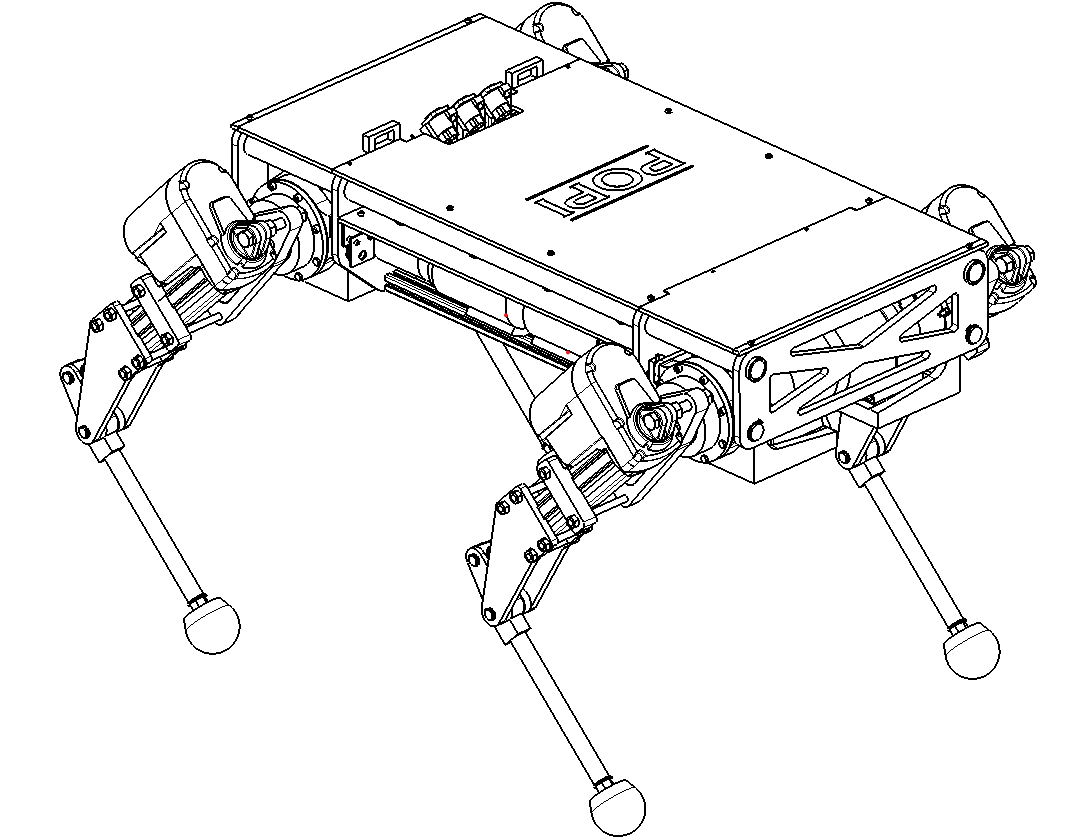
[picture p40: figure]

# MKX 3

# NOTICE DE MONTAGE

# PIECES

N° | Pièce | Quantité
1 | Rail Elcom | 2
2 | Fixations Elcom | 4
3 | Support Moteur Aile | 4
4 | Plaque Verticale Interne | 2
5 | Tube Structure | 2
6 | Moteur Aile - MR977 63 1/96 | 4
7 | Clavette Moteur Aile | 4
8 | Porte Réducteur | 4
9 | Biellette Aile | 4
10 | Liaison Moteur Aile | 4
11 | Plaque Verticale Extérieure | 2
12/13 | Porte Vérin Haut A /Symétrique | 2+2
14/15 | Porte Vérin Haut B /Symétrique | 2+2
16 | Réducteur – PLE060 | 4
17 | Vérin – TiMOTION MA2 | 4
18/19 | Porte Vérin Haut C /Symétrique | 2+2
20 | Pied | 4
21 | Tube Patte | 4
22 | Double Pivot | 4
23 | Biellette Coude | 4
24/25 | Porte Vérin Bas /Symétrique | 4+4
26 | Entretoise Coude | 8
27 | Cale Réducteur | 4
28 | Porte Moteur Épaule | 4
29 | Moteur Épaule – MY1016 350W | 4
30 | Œillet Moteur | 4
31 | Roue Codeuse | 4
32 | Bague Réducteur | 4
33 | Cale Bague Réducteur | 4
34 | Support Capteur Épaule | 4
35 | Plaque Électronique | 1
36 | Équerre | 4
37 | Entretoise Potentiomètre | 8
38 | Support Potentiomètre | 4
39/40/41 | Bornier Type A/B/C | 1+1+1
42 | Maintien Bornier | 3
43 | Accroche Ombilic | 2
44 | Plaque de Protection | 1
45/46 | Cache Moteurs | 1+1
47 | Poignée | 4

# VISSERIE

N° | Type | Quantité
101 | M3x10 Cruciform | 8
102 | M5x16 Slotted Cheese Head | 20
103 | M4x10 Hex Socket Set with Flat Point | 20
104 | M6x25 Hexagon Socket Countersunk Head | 28
105 | M12x90 Hexagon Head | 4
106 | M8x115 Threaded Rod | 8
107 | M8x75 Threaded Rod | 16
108 | M5x40 Hexagon Socket Head Cap | 16
109 | M5x60 Hexagon Head | 16
110 | M4x16 Hexagon Socket Head Cap Special | 4
111 | M6x35 Hexagon Socket Head Cap | 16
112 | M3x25 Hexagon Socket Head Cap | 8
113 | M5x25 Hexagon Socket Head Cap | 4
114 | M5x50 Hexagon Socket Head Cap | 3
115 | M4x14 Hexagon Socket Head Cap | 4
116 | M4x16 Hexagon Socket Head Cap | 16

# AXES

N° | Type | Quantité
201 | Stub D10 L20 | 4
202 | Stub D10 L20 taraudé M5 | 4
203 | Axe D20 L29.5 épaulement + rainure circlips | 4
204 | Axe D20 L28 épaulement + rainure circlips | 4
205 | Axe D12 L27.2 + 2 rainures circlips | 4
206 | Axe D12.8 L35 + 2 rainures circlips | 4
207 | Axe D12 L66.8 + 2 rainures circlips | 4

# CIRCLIPS

N° | Type | Quantité
301 | D3=20 Ep1 | 8
302 | D3=12 Ep1 | 24

Prévoir un nombre important d’écrous et rondelles M4/M5/M6/M8 en conséquence ainsi que 8 écrous et rondelles M12. Respecter idéalement les couples de serrage de la norme E25-030.

# OUTILS NÉCESSAIRES

- Clé de 8, 13 et 16
- Clé à pipe de 8, 13 et 16
- Clé allen de 2, 2.5, 4 et 5
- Tournevis plat de différentes tailles (de petite à grande empreinte)
- Pince circlips extérieur
- Extracteur arrache moyeu
- Maillet

Dans l’assemblage du robot, l’assemblage du corps (étapes 1 à 7) et l’assemblage de la patte (étapes 8 à 12) peuvent être effectuées en parallèle par 2 à 4 personnes.

# ASSEMBLAGE DU CORPS

1.

2.

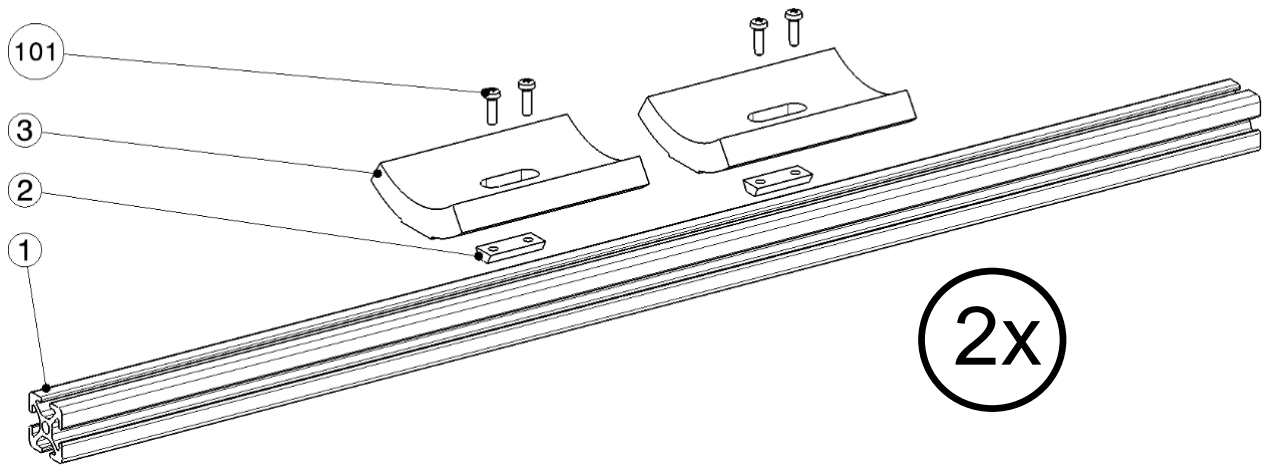
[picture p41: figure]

Insérer 2 dans 1 par les rails.
Laisser idéalement un espace de 35mm entre les deux supports 3 autour du centre. Visser jusqu’à ce que les 3 ne puissent plus translater sur la barre.
Insérer | 5 | dans | 4 | sans | forcer,
progressivement.
Laisser un espace de 17cms entre le bout du tube 5 et la 1ère plaque 4 ainsi qu’un espace d’au moins 48cms entre les deux plaques 4 une fois celles-ci insérées.

3.

4x

4.

5.

Fixer 1 à 4 par la vis 102 de chaque côté des 2 barres avec une rondelle M5.

Encastrer la clavette 7 dans l’arbre du moteur 6.
Déposer du frein faible sur les vis 102 (type GISS Colles).
Fixer le moteur 6 à 4 par les vis 102, en orientant la clavette 7 vers le bas.
Il est conseillé d’ajouter des écrous entre 6 et 4 sur les vis 102 pour un meilleur maintient.

Il est possible que ce sous-ensemble ne soit pas démonté et déjà disponible pour le montage.

Disposer 9 dans 10.
Encastrer 201 au travers de 9 et 10. Disposer 9 dans 8.
Encastrer 202 au travers de 8 et 10. Visser 103 dans 8 et 9 afin de bloquer les axes en rotation par rapport à 8 et 9.

4x

6.

7.

Insérer le sous-ensemble précédent sur l’arbre et la clavette 6 et 7 par la pièce 10, d’abord doucement sans trop forcer, une fois 10 engagé, on peut forcer jusqu’à ce que 8 touche le palier de la plaque 4.
Mettre 301 sur 203.
Insérer 203 dans 8 au travers du palier de 4 sans forcer.
Serrer fortement 203 dans 8 avec 103.

Mettre les 301 dans les rainures des 204.
Insérer la plaque 11 dans les tubes 5 sans forcer, progressivement, en avançant un côté après l’autre (centimètre par centimètre) jusqu’à ce que 11 arrive à fleur des deux 8.
Insérer 204 dans 8 au travers de 11 sans forcer.
Serrer fortement 204 dans 8 avec 103.

# ASSEMBLAGE DE LA PATTE

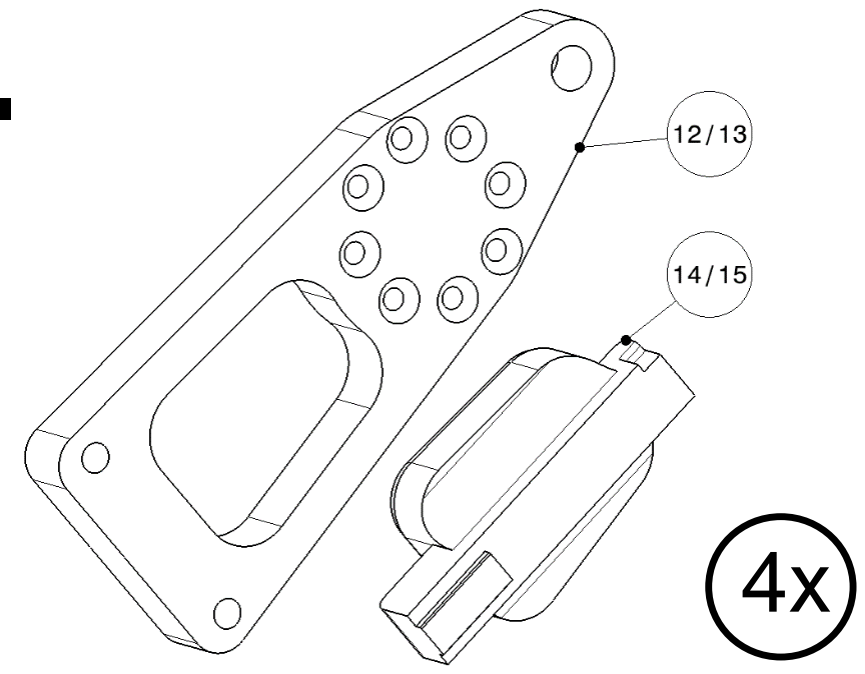
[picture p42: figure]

8.

9.

Insérer 14/15 dans 12/13, attention, les deux pièces ont leurs symétriques différents, bien observer la forme de la poche de 12/13 et du contour de 14/15 afin de former les bonnes paires. Cette opération peut s’effectuer à l’aide d’une presse si nécessaire, la pièce 14/15 doit être insérée complètement.

Fixer 16 sur 12/13 avec les vis 104. Serrer fortement. Mettre seulement 7 vis pour les 8 trous, car un des trous du réducteur 16 n’est pas taraudé, laisser ce trou sans vis sous la pièce

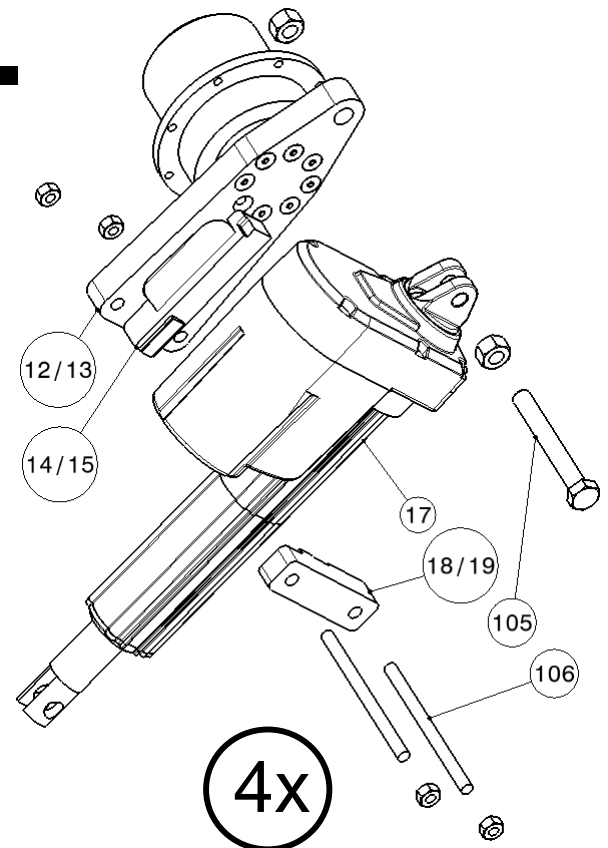
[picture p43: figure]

10.

11.

Fixer le haut du vérin 17 par 105 au travers de 12/13 et 17. Positionner un écrou sur 105 entre 17 et 12/13 ainsi qu’un autre derrière 12/13. Ajouter une rondelle devant chaque écrou. Ne pas serrer la vis dans un premier temps.

Positionner la rainure de 18/19 sur les rails de 17, attention 18/19 a son symétrique différent, deux d’entre elles une poche de plus pour laisser passer le câble des vérins qui seront côté droit du robot.

Fixer le bas de 17 par les vis 106 au travers de 18/19 et 12/13. Ajouter une rondelle M8 sous chaque écrou. Serrer fortement.

Serrer fortement 105 et ses écrous.

Fixer le pied 20 au tube 21. La morphologie du pied peut changer suivant les besoins, le pieds type actuel est vissé dans 21 avec une rondelle M12 intermédiaire.

Fixer 21 dans 22 selon la même méthode. Attention, 22 peut se fixer dans les deux sens mais seul le sens représenté ici est valide (arrondi vers l’intérieur du coude, découpe en biais vers l’extérieur).

Assembler 23 dans 22 et 17 avec respectivement 205 et 206. Mettre les circlips 302 de chaque côté des axes pour bloquer la translation.

12.

Insérer 207 au travers de respectivement 24, 26, 22, 26 et 25. Mettre les circlips 302 de chaque côté des axes pour bloquer la translation.
Positionner les rainures de 24 et 25 dans les rails de 17.

Fixer 24 et 25 à 17 par les tiges filetées 107 et leurs écrous. Peu serrer pour pouvoir ensuite coulisser 24 et 25 le long des rails de 17 jusqu’à ce que les faces de 24 et 18/19 qui se font face, soient distantes de 55,5mm (mesurer au réglet pendant l’ajustement). Serrer progressivement les différents écrous en conservant le décalage de 55,5mm. Ajouter une rondelle M8 sous chaque écrou.

# ASSEMBLAGE FINAL

13.

14.

Fixer la patte au corps par les vis 108 et leurs écrous au travers de 16, 27 et 8, ajouter une rondelle M5 pour la tête de vis ainsi qu’une autre côté écrou.
Les 4 vis 108 doivent être positionnées sur les 4 trous les plus haut des 8 trous présents sur 8.

Fixer le porte moteur 28 à 8 par les vis 109 et leurs écrous, ajouter une rondelle M5 pour la tête de vis ainsi qu’une autre côté écrou.

4x

4x

Insérer l’œillet 30 jusqu’au bout de l’arbre moteur 29, petit diamètre d’abord.

Positionner la cale 33 à l’intérieur du réducteur 16, insérer ensuite la bague par-dessus. La bague dépassera légèrement. Insérer la roue 31 sur la bague 32 en positionnant l’ergot dans la fente de la bague. Maintenir ainsi 31 dans 32 face contre 16 afin qu’elle ne tombe pas. Insérer l’arbre 29 dans 16 au travers de 31, 32 et 33 sans forcer. Pour faciliter l’insertion on peut maintenir plaqué en forçant 29 contre 28 pendant l’insertion. Serrer fortement 110 dans son logement.

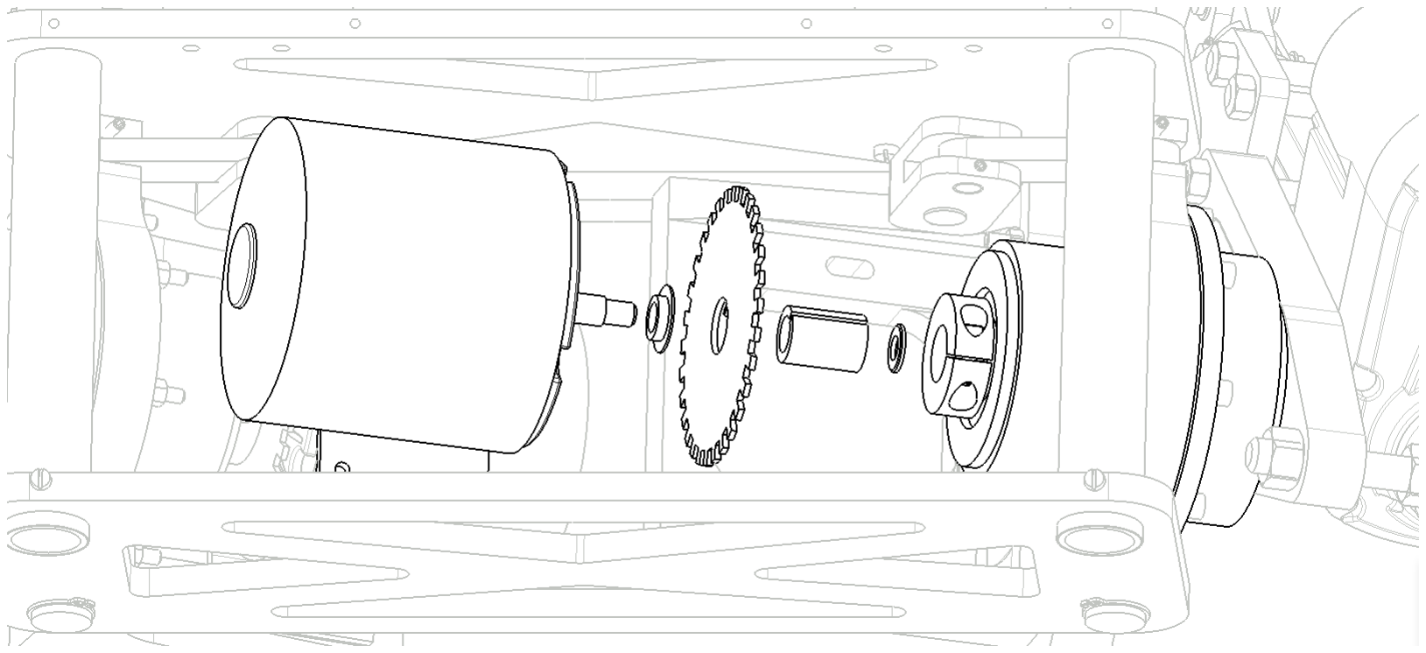
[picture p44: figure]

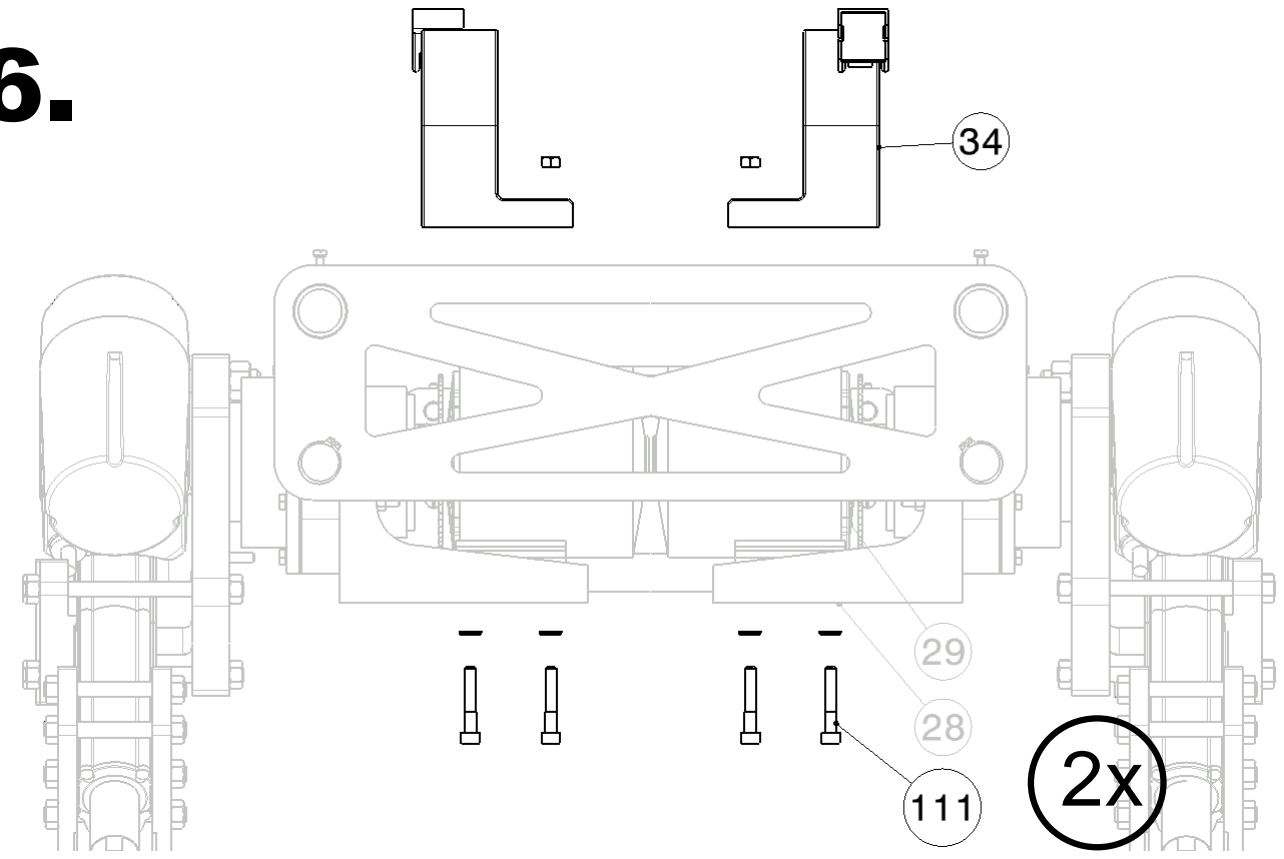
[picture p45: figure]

16.

17.

Positionner 34 autour de 29 en utilisant l’élasticité de 34. La roue codeuse doit se retrouver dans le U formé par le capteur présent sur 34. Fixer 34 à 29 par les vis 111 et son écrou à travers 28, 29 et
34. Seulement 2 vis sont nécessaires au bon maintien de 34, mais elles doivent être positionnées en diagonale l’une de l’autre. Ajouter une rondelle M5 du côté de la tête de vis. Serrer faiblement.

Insérer la plaque électrique 35 sous les tubes 5 (on ne peut pas monter 35 après fixation de l’équerre 36). Fixer 36 sur la plaque 4 par les vis 112 à travers 38, 37 et 36. Serrer modérément de manière à ne pas trop déformer les entretoises 37.

18.

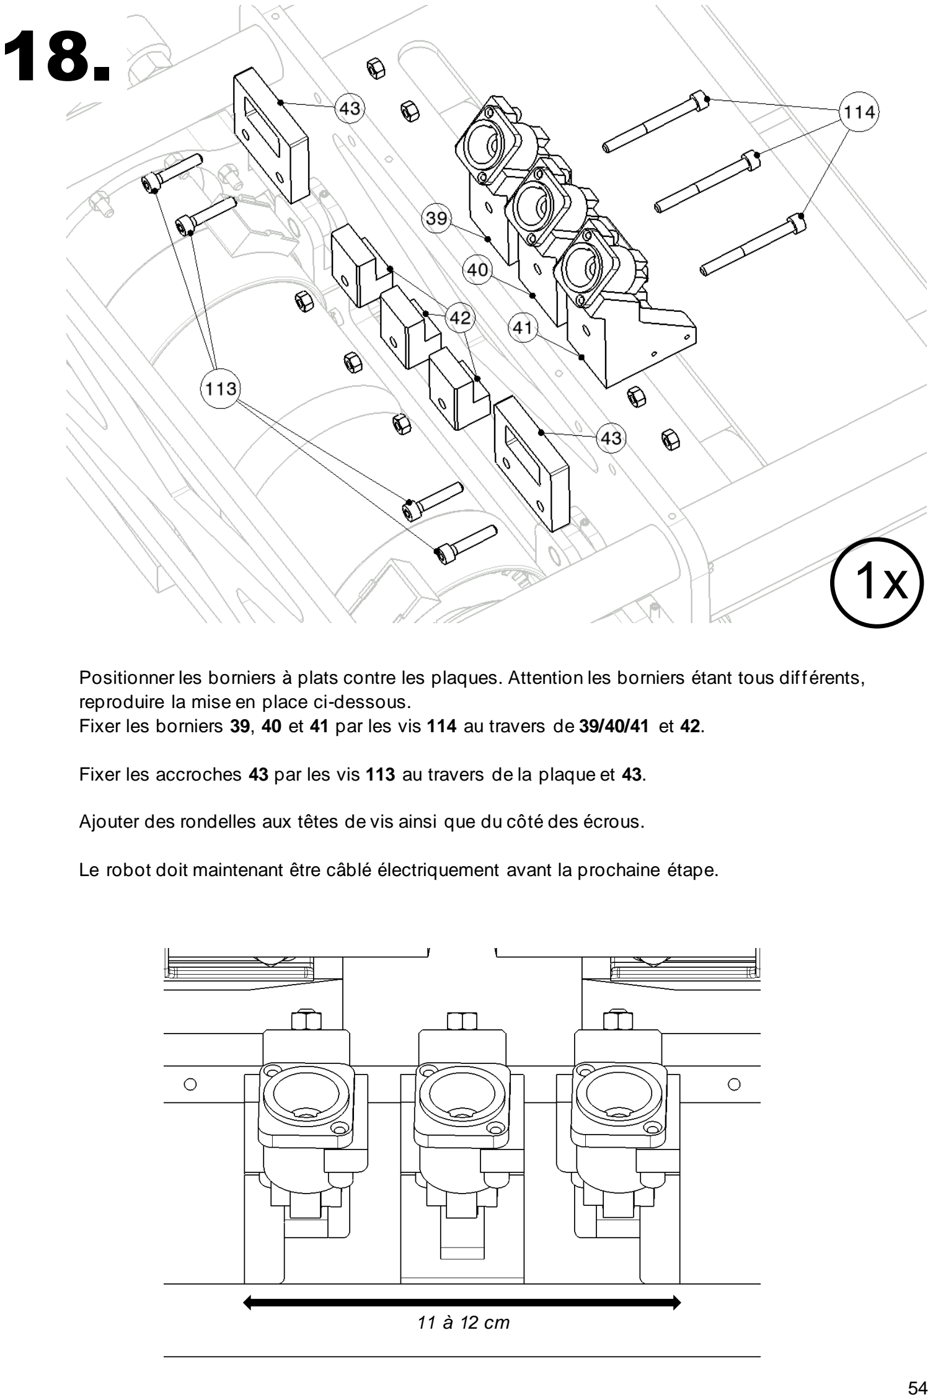
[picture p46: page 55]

Positionner les borniers à plats contre les plaques. Attention les borniers étant tous différents, reproduire la mise en place ci-dessous.
Fixer les borniers 39, 40 et 41 par les vis 114 au travers de 39/40/41 et 42.

Fixer les accroches 43 par les vis 113 au travers de la plaque et 43.

Ajouter des rondelles aux têtes de vis ainsi que du côté des écrous.

Le robot doit maintenant être câblé électriquement avant la prochaine étape.

11 à 12 cm

1x

19.

20.

Fixer les vis 116 à la plaque 44 par des écrous. Ces vis serviront simplement à reposer la plaque sur les tubes. Fixer les plaques plexiglass 45 et 46 aux plaques 4 et 11 par les vis 115. Serrer faiblement.

Enjoy.

1x

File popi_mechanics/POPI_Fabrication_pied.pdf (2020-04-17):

## Fabrication des pieds – POPI

La problématique était de trouver une solution pour les pieds du robot quadrupède POPI.

Contraintes :

- Les pieds doivent supporter le poids du robot, soit 70kg
- Les pieds doivent s’adapter au sol quel que soit la position de la patte.
- Les pieds ne doivent pas dérapés

Solution imaginée :

Pour que la surface de contact au sol soit la plus grande, quelle que soit la position de la patte, il faut que le pied ait une forme sphérique et qu’il soit souple.

Pour que le poids du robot soit supporté il faut que le pied soit suffisamment robuste

Pour que le pied soit antidérapant il faut que la surface du pied soit dans un matériau qui adhère

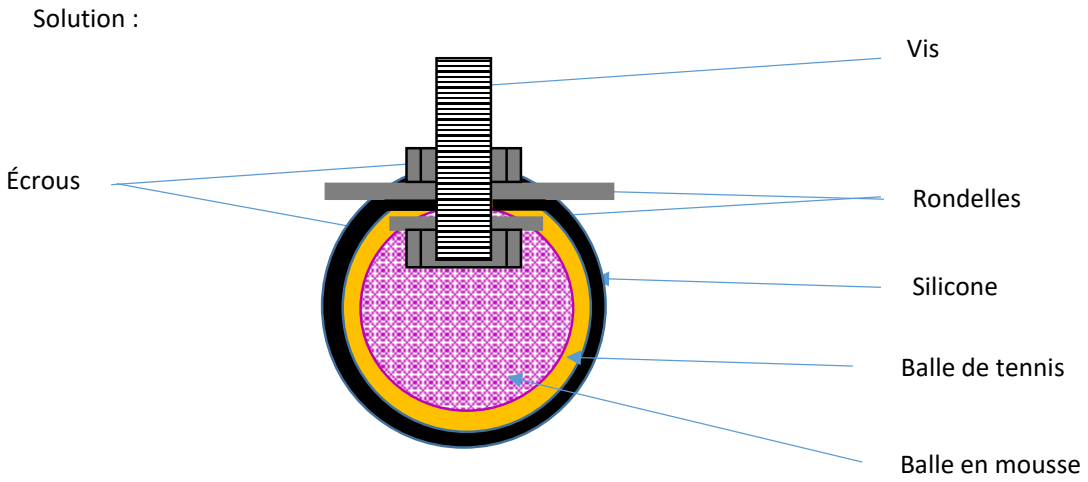
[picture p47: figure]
Solution :; Vis; Écrous; Rondelles; Silicone; Balle de tennis; Balle en mousse

La balle de tennis a une taille et une rigidité adéquate. La balle en mousse permet l’amortissement du pied. Le revêtement en silicone permet une bonne adhérence.

Les 2 rondelles permettent un maintien de l’ensemble.

Lorsque le pied est en pression, l’écrou appuie sur la mousse, qui se compresse à l’intérieur de la balle de tennis.

Fabrication :

1 - Poncer une balle de tennis, et couper le dessus.

2- Insérer la balle en mousse à l’intérieur de la balle de tennis. Le talc permet de facilité l’étape.

3- Mettre la rondelle interne ainsi qu’un écrou sur la vis, l’écrou permet de bloquer la rondelle. Et insérer l’ensemble vis/rondelle dans la balle.

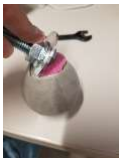
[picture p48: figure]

4- Enlever l’écrou, mettre la seconde rondelle, remettre l’écrou et serrer

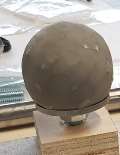
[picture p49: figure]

5- Enduire la balle de silicone, et poncer après séchage. Visser le pied sur la patte.

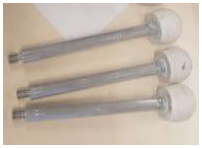
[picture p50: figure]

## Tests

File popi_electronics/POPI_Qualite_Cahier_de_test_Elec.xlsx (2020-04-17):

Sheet: Synthèse Fiche de test
 |  | Fiche de test
FAT N° |  |  | Date :
Version fiche de test:
Contexte : | Essais du sous_enssemble base mobile du RICA IV
Projet : | RICA IV
Unité de code testé
Description |  |  | Version
 |  |  | Test 1 |  | Test 2 | Test 3
Programme
Electronique
Mécanique
Objectif du test
L'objectif du test est de contrôler le bon fonctionnement de l'alimentation. Les pré-requis à la réalisation de cette fiche sont : 1 - Avoir pris connaissance des documents de conception détaillée 2 - Avoir pris connaissance des schéma de câblage des différentes parties 3 - Se munir d'un multimètre
Observations
Descritpion des attendus
Pour considérer le test CONFORME, tous les points de test doivent être OK. 1 - Validation du câblage au travers des tests de continuité 2 - Validation de la bonne tension sur les différent bornier
Bilan des corrections à apporter
Conclusion du test
Conforme |  |  |  | Non conforme

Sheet: Tests Alimentation
 |  | Fiche de test
Nom du projet : EPURE
FAT N° |  |  | Date :
Session :
Fonction :
Contexte :
Projet :
Test | Platine d'alimentation
 | Résultats attendus |  |  | Résultats | Obs. (*)
Test 1 | Allumée L'alimentation
 | Vérifier que le voyant 230 V est allumé |  |  | Res:
 | Vérifier la présence de tension au bornier d'entrée |  |  | Res:
 | Mesurer la tension au bornier d'entrée |  |  | Res:
 | Vérifier la présence de tension au bornier sortie |  |  | Res:
 | Mesurer la tension au bornier de sortie |  |  | Res:
 | Eteindre L'alimentation
 | Vérifier que le voyant 230 V est éteint |  |  | Res:
 | Vérifier la présence de tension au bornier d'entrée |  |  | Res:
 | Mesurer la tension au bornier d'entrée |  |  | Res:
 | Vérifier la présence de tension au bornier sortie |  |  | Res:
 | Mesurer la tension au bornier de sortie |  |  | Res:
Test 2 | Allumée L'alimentation
 | Vérifier que le voyant 24 V est éteint |  |  | Res:
 | Vérifier la présence de tension au bornier d'entrée |  |  | Res:
 | Mesurer la tension au bornier d'entrée |  |  | Res:
 | Permuter l'intérupteur 24V sur ON
 | Vérifier que le voyant 24 V est allumé |  |  | Res:
 | Vérifier la présence de tension au bornier d'entrée |  |  | Res:
 | Mesurer la tension au bornier d'entrée |  |  | Res:
 | Vérifier la présence de tension au bornier sortie |  |  | Res:
 | Mesurer la tension au bornier de sortie |  |  | Res:
 | Permuter l'intérupteur 24V sur OFF
 | Vérifier que le voyant 24 V est éteint |  |  | Res:
 | Vérifier la présence de tension au bornier d'entrée |  |  | Res:
 | Mesurer la tension au bornier d'entrée |  |  | Res:
 | Vérifier la présence de tension au bornier sortie |  |  | Res:
 | Mesurer la tension au bornier de sortie |  |  | Res:

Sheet: Interface de commande
 |  | Fiche de test
Nom du projet : RICA IV
FAT N° |  |  | Date :
Session :
Fonction : | Tests de continuité
Contexte :
Projet :
Test | Interface de commande
 | Résultats attendus |  |  | Résultats | Obs. (*)
CI | Sans allumer l'alimentation
 | Placer le multimètre en mode continuité
Hub USB
Test 1 | Se placer sur le 0V au bornier 230V
 | Se placer sur le - du cable d'alimtation du Hub USB
 | le multimètre émet un signal sonore |  |  | Res:
 | Se placer sur le + du cable d'alimtation du Hub USB
 | le multimètre n'émet aucun signal sonore |  |  | Res:
Test 2 | Avec une pin prendre le 230V au bornier 230V
 | Se placer sur le - du cable d'alimtation du Hub USB
 | le multimètre n'émet aucun signal sonore |  |  | Res:
 | Se placer sur le + du cable d'alimtation du Hub
 | le multimètre émet un signal sonore |  |  | Res:
Raspberry PI B+
Test 3 | Tester le cable d'alimentation
 | le multimètre émet un signal sonore |  |  | Res:
Test 3 | Tester le cable d'alimentation
 | le multimètre émet un signal sonore |  |  | Res:
BeagleBone Black Droite
Test 4 | Tester le cable d'alimentation
 | le multimètre émet un signal sonore |  |  | Res:
Test 6 | Se placer sur la pin P9.32
 | Se placer sur le VccRvarAileAVD
 | le multimètre émet un signal sonore |  |  | Res:
 | Se placer sur le VccRvarCoudeAVD
 | le multimètre émet un signal sonore |  |  | Res:
 | Se placer sur le VccRvarAileAVD
 | le multimètre émet un signal sonore |  |  | Res:
 | Se placer sur le VccRvarCoudeAVD
 | le multimètre émet un signal sonore |  |  | Res:
 | Se placer sur le VccRvarAileARD
 | le multimètre émet un signal sonore |  |  | Res:
 | Se placer sur le VccRvarCoudeARD
 | le multimètre émet un signal sonore |  |  | Res:
Test 7 | Se placer sur la pin P9.1
 | Se placer sur le VccRvarAileAVD
 | le multimètre n'émet un signal sonore |  |  | Res:
 | Se placer sur le VccRvarCoudeAVD
 | le multimètre n'émet un signal sonore |  |  | Res:
 | Se placer sur le VccRvarAileAVD
 | le multimètre n'émet un signal sonore |  |  | Res:
 | Se placer sur le VccRvarCoudeAVD
 | le multimètre n'émet un signal sonore |  |  | Res:
 | Se placer sur le VccRvarAileARD
 | le multimètre n'émet un signal sonore |  |  | Res:
 | Se placer sur le VccRvarCoudeARD
 | le multimètre n'émet un signal sonore |  |  | Res:
Test 8 | Se placer sur la pin P9.1
 | Se placer sur le GNDRvarAileAVD
 | le multimètre émet un signal sonore |  |  | Res:
 | Se placer sur le GNDRvarCoudeAVD
 | le multimètre émet un signal sonore |  |  | Res:
 | Se placer sur le GNDRvarAileAVD
 | le multimètre émet un signal sonore |  |  | Res:
 | Se placer sur le GNDRvarCoudeAVD
 | le multimètre émet un signal sonore |  |  | Res:
 | Se placer sur le GNDRvarAileARD
 | le multimètre émet un signal sonore |  |  | Res:
 | Se placer sur le GNDRvarCoudeARD
 | le multimètre émet un signal sonore |  |  | Res:
Test 9 | Se placer sur la pin P9.5
 | le multimètre n'émet un signal sonore |  |  | Res:
 | Se placer sur la pin P9.5
 | le multimètre n'émet un signal sonore |  |  | Res:
 | Se placer sur la pin P8.13
 | Se placer sur le PWMCoudeAvD
 | le multimètre émet un signal sonore |  |  | Res:
Test 11 | Se placer sur la pin P8.19
 | Se placer sur le PWMCoudeArD
 | le multimètre émet un signal sonore |  |  | Res:
Test 12 | Se placer sur la pin P8.35
 | Se placer sur le DATA-Courant-1-AVD
 | le multimètre émet un signal sonore |  |  | Res:
Test 13 | Se placer sur la pin P8.37
 | Se placer sur le DATA-Courant-2-AVD
 | le multimètre émet un signal sonore |  |  | Res:
Test 14 | Se placer sur la pin P8.39
 | Se placer sur le DATA-Courant-3-AVD
 | le multimètre émet un signal sonore |  |  | Res:
Test 15 | Se placer sur la pin P8.41
 | Se placer sur le DIR-Epaule-AVD
 | le multimètre émet un signal sonore |  |  | Res:
Test 16 | Se placer sur la pin P8.42
 | Se placer sur le DIR-Aile-AVD
 | le multimètre émet un signal sonore |  |  | Res:
Test 17 | Se placer sur la pin P8.43
 | Se placer sur le DIR-Coude-AVD
 | le multimètre émet un signal sonore |  |  | Res:
Test 18 | Se placer sur la pin P8.36
 | Se placer sur le DATA-Courant-1-ARD
 | le multimètre émet un signal sonore |  |  | Res:
Test 19 | Se placer sur la pin P8.38
 | Se placer sur le DATA-Courant-2-ARD
 | le multimètre émet un signal sonore |  |  | Res:
Test 20 | Se placer sur la pin P8.40
 | Se placer sur le DATA-Courant-3-ARD
 | le multimètre émet un signal sonore |  |  | Res:
Test 21 | Se placer sur la pin P8.45
 | Se placer sur le DIR-Epaule-ARD
 | le multimètre émet un signal sonore |  |  | Res:
Test 22 | Se placer sur la pin P8.44
 | Se placer sur le DIR-Aile-ARD
 | le multimètre émet un signal sonore |  |  | Res:
Test 23 | Se placer sur la pin P8.46
 | Se placer sur le DIR-Coude-ARD
 | le multimètre émet un signal sonore |  |  | Res:
Test 24 | Se placer sur la pin P9.14
 | Se placer sur le PWM-Epaule-AVD
 | le multimètre émet un signal sonore |  |  | Res:
Test 25 | Se placer sur la pin P9.16
 | Se placer sur le PWM-Epaule-ARD
 | le multimètre émet un signal sonore |  |  | Res:
Test 26 | Se placer sur la pin P9.21
 | Se placer sur le PWM-Aile-ARD
 | le multimètre émet un signal sonore |  |  | Res:
Test 27 | Se placer sur la pin P9.22
 | Se placer sur le PWM-Aile-AVD
 | le multimètre émet un signal sonore |  |  | Res:
Test 28 | Se placer sur la pin P9.27
 | Se placer sur le SPI-CS1-QECD
 | le multimètre émet un signal sonore |  |  | Res:
Test 29 | Se placer sur la pin P9.28
 | Se placer sur le SPI-CS2-QECD
 | le multimètre émet un signal sonore |  |  | Res:
Test 30 | Se placer sur la pin P9.29
 | Se placer sur le SP-MOSI-QECD
 | le multimètre émet un signal sonore |  |  | Res:
Test 31 | Se placer sur la pin P9.30
 | Se placer sur le SPI-MISO-QECD
 | le multimètre émet un signal sonore |  |  | Res:
Test 32 | Se placer sur la pin P9.31
 | Se placer sur le SCK-CS2-QECD
 | le multimètre émet un signal sonore |  |  | Res:
Test 33 | Se placer sur la pin P9.37
 | Se placer sur le ANA-Coude-Potar-ARD
 | le multimètre émet un signal sonore |  |  | Res:
Test 34 | Se placer sur la pin P9.38
 | Se placer sur le ANA-Aile-Potar-ARD
 | le multimètre émet un signal sonore |  |  | Res:
Test 35 | Se placer sur la pin P9.39
 | Se placer sur le ANA-Coude-Potar-AVD
 | le multimètre émet un signal sonore |  |  | Res:
Test 36 | Se placer sur la pin P9.40
 | Se placer sur le ANA-Aile-Potar-AVD
 | le multimètre émet un signal sonore |  |  | Res:
BeagleBone Black Gauche
Test 37 | Tester le cable d'alimentation
 | le multimètre émet un signal sonore |  |  | Res:
Test 38 | Se placer sur la pin P9.32
 | Se placer sur le VccRvarAileAVG
 | le multimètre émet un signal sonore |  |  | Res:
 | Se placer sur le VccRvarCoudeAVG
 | le multimètre émet un signal sonore |  |  | Res:
 | Se placer sur le VccRvarAileAVG
 | le multimètre émet un signal sonore |  |  | Res:
 | Se placer sur le VccRvarCoudeAVG
 | le multimètre émet un signal sonore |  |  | Res:
 | Se placer sur le VccRvarAileARG
 | le multimètre émet un signal sonore |  |  | Res:
 | Se placer sur le VccRvarCoudeARG
 | le multimètre émet un signal sonore |  |  | Res:
Test 39 | Se placer sur la pin P9.1
 | Se placer sur le VccRvarAileAVG
 | le multimètre n'émet un signal sonore |  |  | Res:
 | Se placer sur le VccRvarCoudeAVG
 | le multimètre n'émet un signal sonore |  |  | Res:
 | Se placer sur le VccRvarAileAVG
 | le multimètre n'émet un signal sonore |  |  | Res:
 | Se placer sur le VccRvarCoudeAVG
 | le multimètre n'émet un signal sonore |  |  | Res:
 | Se placer sur le VccRvarAileARG
 | le multimètre n'émet un signal sonore |  |  | Res:
 | Se placer sur le VccRvarCoudeARG
 | le multimètre n'émet un signal sonore |  |  | Res:
Test 40 | Se placer sur la pin P9.1
 | Se placer sur le GNDRvarAileAVG
 | le multimètre émet un signal sonore |  |  | Res:
 | Se placer sur le GNDRvarCoudeAVG
 | le multimètre émet un signal sonore |  |  | Res:
 | Se placer sur le GNDRvarAileAVG
 | le multimètre émet un signal sonore |  |  | Res:
 | Se placer sur le GNDRvarCoudeAVG
 | le multimètre émet un signal sonore |  |  | Res:
 | Se placer sur le GNDRvarAileARG
 | le multimètre émet un signal sonore |  |  | Res:
 | Se placer sur le GNDRvarCoudeARG
 | le multimètre émet un signal sonore |  |  | Res:
Test 41 | Se placer sur la pin P9.32
 | le multimètre n'émet un signal sonore |  |  | Res:
Test 42 | Se placer sur la pin P8.13
 | Se placer sur le PWMCoudeAvG
 | le multimètre émet un signal sonore |  |  | Res:
Test 43 | Se placer sur la pin P8.19
 | Se placer sur le PWMCoudeArG
 | le multimètre émet un signal sonore |  |  | Res:
Test 44 | Se placer sur la pin P8.35
 | Se placer sur le DATA-Courant-1-AVG
 | le multimètre émet un signal sonore |  |  | Res:
Test 45 | Se placer sur la pin P8.37
 | Se placer sur le DATA-Courant-2-AVG
 | le multimètre émet un signal sonore |  |  | Res:
Test 46 | Se placer sur la pin P8.39
 | Se placer sur le DATA-Courant-3-AVG
 | le multimètre émet un signal sonore |  |  | Res:
Test 47 | Se placer sur la pin P8.41
 | Se placer sur le DIR-Epaule-AVG
 | le multimètre émet un signal sonore |  |  | Res:
Test 48 | Se placer sur la pin P8.42
 | Se placer sur le DIR-Aile-AVG
 | le multimètre émet un signal sonore |  |  | Res:
Test 49 | Se placer sur la pin P8.43
 | Se placer sur le DIR-Coude-AVG
 | le multimètre émet un signal sonore |  |  | Res:
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

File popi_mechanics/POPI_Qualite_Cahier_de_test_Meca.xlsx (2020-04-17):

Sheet: Synthèse Fiche de test
 |  | Fiche de test
FAT N° |  |  | Date :
Version fiche de test:
Contexte : | Essais du sous_enssemble base mobile du RICA IV
Projet : | RICA IV
Unité de code testé
Description |  |  | Version
 |  |  | Test 1 |  | Test 2 | Test 3
Programme
Electronique
Mécanique
Objectif du test
L'objectif du test est de contrôler la conformité des pièces après usinage. Les pré-requis à la réalisation de cette fiche sont : 1 - Avoir pris connaissance des documents de conception détaillée 2 - Avoir une balance d'incertitude max de 1g 3 - Se munir d'un réglet de longeueur 30cm et d'incertitude max de 0,5 mm 4 - Se munir d'un pied à coulisse d'incertitude max de 0,2 mm
Observations
Descritpion des attendus
Pour considérer le test CONFORME, tous les points de test doivent être OK. 1 - Validation des mesures de tolérence 1 mm au réglet 2- Validation des mesures de tolérence 0.5 mm au pied à coulisse
Bilan des corrections à apporter
Conclusion du test
Conforme |  |  |  | Non conforme

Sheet: Plaque Verticale int
 |  | Fiche de test
Nom du projet : RICA IV
FAT N° |  |  | Date :
Session :
Fonction : | Test métrologie
Contexte :
Projet :
Test | Pièce N° 04 : Plaque verticale intérieure
 | Résultats attendus |  |  | Résultats | Obs. (*)
Avant
Test 1 | Venir mesurer la longueur "a"
 | On Mesure 173 ± 1 mm |  |  | Res:
 | Venir mesurer la longueur "b"
 | On Mesure 399 ± 1 mm |  |  | Res:
 | Venir mesurer la longueur "c"
 | On Mesure 10 ± 0.5 mm |  |  | Res:
 | Venir mesurer la longueur "d"
 | On Mesure 148 ± 1 mm |  |  | Res:
 | Venir mesurer la longueur "e"
 | On Mesure 5 ± 0.5 mm |  |  | Res:
 | Venir mesurer la longueur "f"
 | On Mesure 28 ± 1 mm |  |  | Res:
 | Venir mesurer la longueur "g"
 | On Mesure 20 ± 1 mm |  |  | Res:
Arrière
Test 2 | Venir mesurer la longueur "a"
 | On Mesure 173 ± 1 mm |  |  | Res:
 | Venir mesurer la longueur "b"
 | On Mesure 399 ± 1 mm |  |  | Res:
 | Venir mesurer la longueur "c"
 | On Mesure 10 ± 0.5 mm |  |  | Res:
 | Venir mesurer la longueur "d"
 | On Mesure 148 ± 1 mm |  |  | Res:
 | Venir mesurer la longueur "e"
 | On Mesure 5 ± 0.5 mm |  |  | Res:
 | Venir mesurer la longueur "f"
 | On Mesure 28 ± 1 mm |  |  | Res:
 | Venir mesurer la longueur "g"
 | On Mesure 20 ± 1 mm |  |  | Res:

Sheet: Porte réducateur
 |  | Fiche de test
Nom du projet : RICA IV
FAT N° |  |  | Date :
Session :
Fonction : | Test métrologie
Contexte :
Projet :
Test | Pièce N° 08 : Porte réducteur
 | Résultats attendus |  |  | Résultats | Obs. (*)
Avant Droit
Test 1 | Peser la pièce
 | On Mesure 242 g |  |  | Res:
 | Sur le plan de la page suivante
 | Venir mesurer la longueur "a"
 | On Mesure 152 ± 1 mm |  |  | Res:
 | Venir mesurer la longueur "b"
 | On Mesure 10 ± 0.5 mm |  |  | Res:
 | Venir mesurer la longueur "c"
 | On Mesure 16 ± 0.5 mm |  |  | Res:
 | Venir mesurer la longueur "d"
 | On Mesure 20 ± 1 mm |  |  | Res:
 | Venir mesurer la longueur "e"
 | On Mesure 8 ± 0.5 mm |  |  | Res:
 | Venir mesurer la longueur "f"
 | On Mesure 16 ± 0.5 mm |  |  | Res:
 | Venir mesurer la longueur "g"
 | On Mesure 10 ± 0.5 mm |  |  | Res:
 | Venir mesurer la longueur "h"
 | On Mesure 47 ± 1 mm |  |  | Res:
 | Venir mesurer la longueur "i"
 | On Mesure 118 ± 1 mm |  |  | Res:
 | Venir mesurer la longueur "j"
 | On Mesure 5,5 ± 0.5 mm |  |  | Res:
 | Venir mesurer la longueur "k"
 | On Mesure 3 ± 0.5 mm |  |  | Res:
Avant Gauche
Test 2 | Peser la pièce
 | On Mesure 242 g |  |  | Res:
 | Sur le plan de la page suivante
 | Venir mesurer la longueur "a"
 | On Mesure 152 ± 1 mm |  |  | Res:
 | Venir mesurer la longueur "b"
 | On Mesure 10 ± 0.5 mm |  |  | Res:
 | Venir mesurer la longueur "c"
 | On Mesure 16 ± 0.5 mm |  |  | Res:
 | Venir mesurer la longueur "d"
 | On Mesure 20 ± 1 mm |  |  | Res:
 | Venir mesurer la longueur "e"
 | On Mesure 8 ± 0.5 mm |  |  | Res:
 | Venir mesurer la longueur "f"
 | On Mesure 16 ± 0.5 mm |  |  | Res:
 | Venir mesurer la longueur "g"
 | On Mesure 10 ± 0.5 mm |  |  | Res:
 | Venir mesurer la longueur "h"
 | On Mesure 47 ± 1 mm |  |  | Res:
 | Venir mesurer la longueur "i"
 | On Mesure 118 ± 1 mm |  |  | Res:
 | Venir mesurer la longueur "j"
 | On Mesure 5,5 ± 0.5 mm |  |  | Res:
 | Venir mesurer la longueur "k"
 | On Mesure 3 ± 0.5 mm |  |  | Res:
Arrière Droit
Test 3 | Peser la pièce
 | On Mesure 242 g |  |  | Res:
 | Sur le plan de la page suivante
 | Venir mesurer la longueur "a"
 | On Mesure 152 ± 1 mm |  |  | Res:
 | Venir mesurer la longueur "b"
 | On Mesure 10 ± 0.5 mm |  |  | Res:
 | Venir mesurer la longueur "c"
 | On Mesure 16 ± 0.5 mm |  |  | Res:
 | Venir mesurer la longueur "d"
 | On Mesure 20 ± 1 mm |  |  | Res:
 | Venir mesurer la longueur "e"
 | On Mesure 8 ± 0.5 mm |  |  | Res:
 | Venir mesurer la longueur "f"
 | On Mesure 16 ± 0.5 mm |  |  | Res:
 | Venir mesurer la longueur "g"
 | On Mesure 10 ± 0.5 mm |  |  | Res:
 | Venir mesurer la longueur "h"
 | On Mesure 47 ± 1 mm |  |  | Res:
 | Venir mesurer la longueur "i"
 | On Mesure 118 ± 1 mm |  |  | Res:
 | Venir mesurer la longueur "j"
 | On Mesure 5,5 ± 0.5 mm |  |  | Res:
 | Venir mesurer la longueur "k"
 | On Mesure 3 ± 0.5 mm |  |  | Res:
Arrière gauche
Test 4 | Peser la pièce
 | On Mesure 242 g |  |  | Res:
 | Sur le plan de la page suivante
 | Venir mesurer la longueur "a"
 | On Mesure 152 ± 1 mm |  |  | Res:
 | Venir mesurer la longueur "b"
 | On Mesure 10 ± 0.5 mm |  |  | Res:
 | Venir mesurer la longueur "c"
 | On Mesure 16 ± 0.5 mm |  |  | Res:
 | Venir mesurer la longueur "d"
 | On Mesure 20 ± 1 mm |  |  | Res:
 | Venir mesurer la longueur "e"
 | On Mesure 8 ± 0.5 mm |  |  | Res:
 | Venir mesurer la longueur "f"
 | On Mesure 16 ± 0.5 mm |  |  | Res:
 | Venir mesurer la longueur "g"
 | On Mesure 10 ± 0.5 mm |  |  | Res:
 | Venir mesurer la longueur "h"
 | On Mesure 47 ± 1 mm |  |  | Res:
 | Venir mesurer la longueur "i"
 | On Mesure 118 ± 1 mm |  |  | Res:
 | Venir mesurer la longueur "j"
 | On Mesure 5,5 ± 0.5 mm |  |  | Res:
 | Venir mesurer la longueur "k"
 | On Mesure 3 ± 0.5 mm |  |  | Res:

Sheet: Bielette aile
 |  | Fiche de test
Nom du projet : RICA IV
FAT N° |  |  | Date :
Session :
Fonction : | Test métrologie
Contexte :
Projet :
Test | Pièce N° 09 : Bielette Aile
 | Résultats attendus |  |  | Résultats | Obs. (*)
Avant droit
Test 1 | Peser la pièce
 | On Mesure 30 g |  |  | Res:
 | Sur le plan de la page suivante
 | Venir mesurer la longueur "a"
 | On Mesure 20 ± 0.5 mm |  |  | Res:
 | Venir mesurer la longueur "b"
 | On Mesure 10 ± 0.5 mm |  |  | Res:
 | Venir mesurer la longueur "c"
 | On Mesure 8 ± 0.5 mm |  |  | Res:
 | Venir mesurer la longueur "d"
 | On Mesure 80 ± 1 mm |  |  | Res:
Arrière droit
Test 2 | Peser la pièce
 | On Mesure 30 g |  |  | Res:
 | Sur le plan de la page suivante
 | Venir mesurer la longueur "a"
 | On Mesure 20 ± 0.5 mm |  |  | Res:
 | Venir mesurer la longueur "b"
 | On Mesure 10 ± 0.5 mm |  |  | Res:
 | Venir mesurer la longueur "c"
 | On Mesure 8 ± 0.5 mm |  |  | Res:
 | Venir mesurer la longueur "d"
 | On Mesure 80 ± 1 mm |  |  | Res:
Avant gauche
Test 3 | Peser la pièce
 | On Mesure 30 g |  |  | Res:
 | Sur le plan de la page suivante
 | Venir mesurer la longueur "a"
 | On Mesure 20 ± 0.5 mm |  |  | Res:
 | Venir mesurer la longueur "b"
 | On Mesure 10 ± 0.5 mm |  |  | Res:
 | Venir mesurer la longueur "c"
 | On Mesure 8 ± 0.5 mm |  |  | Res:
 | Venir mesurer la longueur "d"
 | On Mesure 80 ± 1 mm |  |  | Res:
Arrière gauche
Test 4 | Peser la pièce
 | On Mesure 30 g |  |  | Res:
 | Sur le plan de la page suivante
 | Venir mesurer la longueur "a"
 | On Mesure 20 ± 0.5 mm |  |  | Res:
 | Venir mesurer la longueur "b"
 | On Mesure 10 ± 0.5 mm |  |  | Res:
 | Venir mesurer la longueur "c"
 | On Mesure 8 ± 0.5 mm |  |  | Res:
 | Venir mesurer la longueur "d"
 | On Mesure 80 ± 1 mm |  |  | Res:

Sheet: Liaison aile
 |  | Fiche de test
Nom du projet : RICA IV
FAT N° |  |  | Date :
Session :
Fonction : | Test métrologie
Contexte :
Projet :
Test | Pièce N° 10 : Liaison moteur aile
 | Résultats attendus |  |  | Résultats | Obs. (*)
Avant droit
Test 1 | Peser la pièce
 | On Mesure 67 g |  |  | Res:
 | Sur le plan de la page suivante
 | Venir mesurer la longueur "a"
 | On Mesure 56 ± 0.5 mm |  |  | Res:
 | Venir mesurer la longueur "b"
 | On Mesure 34 ± 0.5 mm |  |  | Res:
 | Venir mesurer la longueur "c"
 | On Mesure 10 ± 0.5 mm |  |  | Res:
 | Venir mesurer la longueur "d"
 | On Mesure 14 ± 0.5 mm |  |  | Res:
 | Venir mesurer la longueur "e"
 | On Mesure 5 ± 0.5 mm |  |  | Res:
 | Venir mesurer la longueur "f"
 | On Mesure 6 ± 0.5 mm |  |  | Res:
 | Venir mesurer la longueur "g"
 | On Mesure 8 ± 0.5 mm |  |  | Res:
 | Venir mesurer la longueur "h"
 | On Mesure 20 ± 0.5 mm |  |  | Res:
Arrière droit
Test 2 | Peser la pièce
 | On Mesure 67 g |  |  | Res:
 | Sur le plan de la page suivante
 | Venir mesurer la longueur "a"
 | On Mesure 56 ± 0.5 mm |  |  | Res:
 | Venir mesurer la longueur "b"
 | On Mesure 34 ± 0.5 mm |  |  | Res:
 | Venir mesurer la longueur "c"
 | On Mesure 10 ± 0.5 mm |  |  | Res:
 | Venir mesurer la longueur "d"
 | On Mesure 14 ± 0.5 mm |  |  | Res:
 | Venir mesurer la longueur "e"
 | On Mesure 5 ± 0.5 mm |  |  | Res:
 | Venir mesurer la longueur "f"
 | On Mesure 6 ± 0.5 mm |  |  | Res:
 | Venir mesurer la longueur "g"
 | On Mesure 8 ± 0.5 mm |  |  | Res:
 | Venir mesurer la longueur "h"
 | On Mesure 20 ± 0.5 mm |  |  | Res:
Avant gauche
Test 3 | Peser la pièce
 | On Mesure 67 g |  |  | Res:
 | Sur le plan de la page suivante
 | Venir mesurer la longueur "a"
 | On Mesure 56 ± 0.5 mm |  |  | Res:
 | Venir mesurer la longueur "b"
 | On Mesure 34 ± 0.5 mm |  |  | Res:
 | Venir mesurer la longueur "c"
 | On Mesure 10 ± 0.5 mm |  |  | Res:
 | Venir mesurer la longueur "d"
 | On Mesure 14 ± 0.5 mm |  |  | Res:
 | Venir mesurer la longueur "e"
 | On Mesure 5 ± 0.5 mm |  |  | Res:
 | Venir mesurer la longueur "f"
 | On Mesure 6 ± 0.5 mm |  |  | Res:
 | Venir mesurer la longueur "g"
 | On Mesure 8 ± 0.5 mm |  |  | Res:
 | Venir mesurer la longueur "h"
 | On Mesure 20 ± 0.5 mm |  |  | Res:
Arrière gauche
Test 4 | Peser la pièce
 | On Mesure 67 g |  |  | Res:
 | Sur le plan de la page suivante
 | Venir mesurer la longueur "a"
 | On Mesure 56 ± 0.5 mm |  |  | Res:
 | Venir mesurer la longueur "b"
 | On Mesure 34 ± 0.5 mm |  |  | Res:
 | Venir mesurer la longueur "c"
 | On Mesure 10 ± 0.5 mm |  |  | Res:
 | Venir mesurer la longueur "d"
 | On Mesure 14 ± 0.5 mm |  |  | Res:
 | Venir mesurer la longueur "e"
 | On Mesure 5 ± 0.5 mm |  |  | Res:
 | Venir mesurer la longueur "f"
 | On Mesure 6 ± 0.5 mm |  |  | Res:
 | Venir mesurer la longueur "g"
 | On Mesure 8 ± 0.5 mm |  |  | Res:
 | Venir mesurer la longueur "h"
 | On Mesure 20 ± 0.5 mm |  |  | Res:
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

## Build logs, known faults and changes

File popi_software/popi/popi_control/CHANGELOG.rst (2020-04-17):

^^^^^^^^^^^^^^^^^^^^^^^^^^^^^^^^^^^^^^^^^^^^^
Changelog for package popi_control
^^^^^^^^^^^^^^^^^^^^^^^^^^^^^^^^^^^^^^^^^^^^^

0.5.0 (2019-09-18)
------------------
* Merge pull request `#20 <https://github.com/PickNikRobotics/popi_control/issues/20>`_ from ipa-mdl/fix-loop-deadlock
  refactor GenericHWControlLoop to a sleep-based loop
* Merge pull request `#19 <https://github.com/PickNikRobotics/popi_control/issues/19>`_ from PaulBouchier/kinetic-devel
  change sim_control_mode to 0 (position) so demo works
* Merge pull request `#21 <https://github.com/PickNikRobotics/popi_control/issues/21>`_ from MohmadAyman/fix_typo
  fixed a typo in readme
* fixed a typo in readme
* refactor GenericHWControlLoop to a sleep-based loop
  using ros:Timer might lead to deadlocks
* initialize desired_update_period\_ (renamed from desired_update_freq\_)
* Revert "Depend on Eigen3"
  This reverts commit 608cc2fd64739ee56c3fbd5a0ae9d5d26b5684d0.
* change sim_control_mode to 0 (position) so demo works
* Merge pull request `#16 <https://github.com/PickNikRobotics/popi_control/issues/16>`_ from lucasw/xml-version
  xml version tags for all launch files.
* xml version tags for all launch files.
* Merge pull request `#15 <https://github.com/PickNikRobotics/popi_control/issues/15>`_ from enricotoi/kinetic-devel
  Fixed a typo in the README.md
* Fixed a typo in the README.md
  popi_simulaton.launch -> popi_simulation.launch
* Update README.md
* Contributors: Dave Coleman, Lucas Walter, Mathias Lüdtke, Paul Bouchier, enrico toivinen, mohmad ayman

0.4.1 (2017-06-20)
------------------
* Changed boost::shared_ptr to typedef for Lunar support
* Implemented simulated velocity control
* Contributors: Dave Coleman

0.4.0 (2016-06-29)
------------------
* Depend on Eigen3
* Remove dependency on meta package
* Fixed var name
* Contributors: Dave Coleman

0.3.1 (2016-01-13)
------------------
* API deprecation fix for rosparam_shortcuts
* Switched to better use of rosparam_shortcuts
* Ability to record all controller status data, not just at certain frequency
* Contributors: Dave Coleman

0.3.0 (2015-12-27)
------------------
* Removed bad reference name
* Switched to using name\_
* Record error data
* Disable soft joint limits
* header to debug output
* Added error checking of control loops time
* Fix init() bug
* Contributors: Dave Coleman

0.2.1 (2015-12-09)
------------------
* Merge branch 'indigo-devel' of github.com:davetcoleman/popi_control into indigo-devel
* Fix install path
* Improve user output message
* Contributors: Dave Coleman

0.2.0 (2015-12-09)
------------------
* Do not automatically call init()
* Removed warning of joint limits for continous joints
* Fix missing variable
* Improved popi_control example package
* Moved popi example code into subdirectory
* Contributors: Dave Coleman

0.1.4 (2015-12-07)
------------------
* Added missing dependency on sensor_msgs
* Contributors: Dave Coleman

0.1.3 (2015-12-05)
------------------
* Fix catkin lint errors
* Added FindGflags directly to this repo
* Minor fix
* Updated README
* Contributors: Dave Coleman

0.1.2 (2015-12-02)
------------------
* Added dependency on gflags
* Contributors: Dave Coleman

0.1.1 (2015-12-02)
------------------
* Added travis support
* Updated README
* Contributors: Dave Coleman

0.1.0 (2015-12-02)
------------------
* Initial release of popi_control
* Contributors: Dave Coleman

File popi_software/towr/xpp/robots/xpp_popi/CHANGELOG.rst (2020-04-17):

^^^^^^^^^^^^^^^^^^^^^^^^^^^^^^^^^
Changelog for package xpp_vis_popi
^^^^^^^^^^^^^^^^^^^^^^^^^^^^^^^^^

1.0.10 (2019-04-05)
-------------------
* add xacro dependency
* Contributors: Alexander Winkler

1.0.9 (2018-07-10)
------------------
* Merge pull request #7 from zlingkang/xacropi2xacro
  change deprecated xacro.py to xacro
* Contributors: zlingkang

1.0.8 (2018-07-07)
------------------
* avoid IK segfault for biped/popi when not enough ee positions sent
* removed limits on popileg joint angles
* Contributors: Alexander Winkler

1.0.7 (2018-07-03)
------------------
* add rviz launch specifically for popi
* Contributors: Alexander Winkler

1.0.6 (2018-04-18)
------------------
* add missing libxpp_popi.so library to catkin install
* Contributors: Alexander Winkler

1.0.5 (2018-02-01)
------------------
* modernize CMake files
* use default keyword for empty destructors
* use default BSD license
* Contributors: Alexander Winkler

1.0.4 (2018-01-03)
------------------
* Merge pull request #3 from leggedrobotics/devel
  Fix xacro bug and remove terrain and optimization specific classes.
* xpp_popi: add --inorder when processing xacro files
  see http://wiki.ros.org/xacro#Processing_Order
* cleaned up formatting of xacro files
* removed unused xacro origin tag causing run failure
* Contributors: Alexander W Winkler

1.0.3 (2017-11-03)
------------------
* removed xpp_ros_conversions (now in xpp_states)
* 1.0.2
* update changelog
* Contributors: Alexander Winkler

1.0.2 (2017-10-28)
------------------

1.0.1 (2017-10-27)
------------------

1.0.0 (2017-10-26)
------------------
* added separate xpp_example package and Readme.md
* included install space in CMakeLists.txt
* explicitly listing ros dependencies (not through catkin_package macro)
* Added license to files and giving credit to contributors.
* cleaned up package.xml and CMakeLists.txt files
* cleaned up endeffector and joint representation
* showed close connection of mono/bi/quad to popi
* added doxygen comments to header files
* made xpp_vis robot independent. Added sample hopper executables
* Contributors: Alexander Winkler

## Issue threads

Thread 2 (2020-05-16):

Motor model

fcaponetto, 2020-05-16:
Hi!
First, I would say that your project is very interesting!

I am curious about the kind of motors you have been using in this project. Are you currently using BLDC motors?

Thanks in andance

popi-mkx3, 2020-05-17:
Hi Fernando,

Thanks for your feedback!

No, our motors are not brushless but brushed.

But this is not the best solution. We prefer to present you our errors and
what we get out of them :

*What we have done ;*

- A fairly heavy and oversized structure (22.5kg without actuators) due to
the imposed raw materials (aluminum and steel), the time that we lacked to
simulate (oversizing), and our lack of experience.

- An underestimated weight constraint in the choice of actuators. The power
to weight ratio being very very important in this area.

- Over-sizing of the initial torque requirement.

- Underestimate the problem of EMI (electromagnetic interference), which is
stronger in brushed motors and which caused us a lot of noise problems at
the end of the project.

This led us to choose heavy brushed motors with a high torque (120Nm) which
essentially serves to compensate for the weight of the actuators themselves
(48kg of actuators).

*What should rather be done;*

*Take BLDCs* that have a better power-to-weight ratio and fewer EMI
problems. Ideally brushless like those used for drones, like T-motors for
example, which are very light.

We are currently designing the Popi V2, our actuators now weigh less than
500 grams compared to the average 4kg for those of the V1. Also, we are now
using much lighter materials for the structure (mostly 3D-printed). These
developments should allow us afterwards to have a new Popi of only 20kg
maximum.

Do not hesitate if you have any question, we will answer with pleasure.

Looking forward to reading you,

POPI Team

Le sam. 16 mai 2020 à 20:54, Fernando Caponetto <notifications@github.com>
a écrit :

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

Closed 2021-03-04.

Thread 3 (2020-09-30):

Popi's Equation of motion in every gaits of legs and base.

UchidaKouki, 2020-09-30:
Hello, everyone.
I have a new question about Popi.
I want to know about Popi's equation of motion in every gaits of legs and base.
I'm a collage student and studying about 4-legged robot simulation.

Popi simulates motion and path of robot by using system of Towr.
I found this repogitory during studying about Towr.
ALEXANDER in ETH Zurich published paper about kinematics of 4-legged robot, Towr and Xpp
He also introduced the paper in his repogitory.

Robot models of Popi is deferent from Xpp, so I searched paper which wrote about Popi, because I want to study Popi's kinematics anew.
But I couldn't find the paper in the web.
I apologize my low level ability of searching paper.

If you published the paper which wrote about Popi's kinematics or equation of motion in formula, can you tell me where is the paper?
If possible, please tell me about Popi's kinematics or equation of motion in this issue?

popi-mkx3, 2020-09-30:
Hello HuchidaKouki,

Sorry about that, we actually did not publish any paper about Popi's kinematics. The equations are located [here](https://github.com/popi-mkx3/popi_project/blob/master/popi_software/towr/xpp/robots/xpp_popi/src/popileg_inverse_kinematics.cc) , just in case you didn't find them.

I actually calculated those equations using the modified Denavit-Hartemberg method, but it was all handwriting, backed up by long-lost Matlab's files. I am currently lacking the time to put the whole work into a numerical format, but I just quickly rewrote the transformation matrix using the modified Denavit-Hartemberg convention, so that you can give it a try. You should easily come up to the solution.

[Transformation matrix.pdf](https://github.com/popi-mkx3/popi_project/files/5305177/Transformation.matrix.pdf)

Please let me know if this is enough to help you. Otherwise I will do my best to find some more time.

With regards,
Lucas

Closed 2021-03-04.

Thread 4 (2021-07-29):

Adding robot model to Towr

Mikipaw, 2021-07-29:
You said that you easily added your robot model in towr. Can you please explain how to do it with my robot unitree a1?

popi-mkx3, 2021-08-02:
Hello Mikipaw ! Thanks for reaching out.

I suggest you have a look [here](https://github.com/popi-mkx3/popi_project/tree/master/popi_software/towr/towr/towr/include/towr/models/examples) to see how different robot models are built.

You could also clone the repository, go to _catkin_ws/src/popi_project/popi_software/towr_ and then use
`grep -rnwi . -e "popi"`

This way you should have more insights on which files we added or modified to have our model working.

I don't remember stating anywhere it was an easy process though, and can't provide a step-by-step method on how to add your own model. You should also have a look at the [doc](http://docs.ros.org/en/melodic/api/towr/html/group__Robots.html) written by Alexander W. Winkler for Towr.

If you have any more questions, please provide some details on what you've tried so far and what problem you encountered. A good way to do this would be to fork Alexander repo (or this repo) and commit your changes so that I can have an in-depth look at your work.
It will prove really difficult to help you otherwise.

Hope this will be of some help for you.

Cheers,
Lucas

Mikhalinho, 2021-08-09:
Hello again!

Can you please give me an example of 3D map where popi creates path using towr?

And how do you send the map to popi?

popi-mkx3, 2021-08-09:
Hi ! Are you the same person ? Did you have any success following my previous message ?

I think you are mistaking about what we did with Towr. We actually didn't do any SLAM or path planning. We used Towr to create joint trajectories for a simple walking gait. Then we saved those trajectories and sent them to the real robot. You'll have more details on the whole process in this [README](https://github.com/popi-mkx3/popi_project/blob/master/popi_software/README.md) if you want.

Hope this helps.
Lucas

popi-mkx3, 2021-08-09:
If you want to have a look at the trajectories created by Towr, here is how we did it.

When running ```roslaunch towr_ros towr_ros_popi.launch```, here is the ```rqt_graph```
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

Basically here is what is going on :
- xpp computes desired states given cost functions, max deviation of the foot from the body, etc. It gives you desired feet positions.
- the urdf_visualizer_popi4 actually reads your URDF and this is where IK is applied to get joint angles. It allows you to see things in RViz. But this wasn't too convenient though, as it was in a xpp_msgs::RobotStateJoint type of message.
- So we wrote a small node, ```joint_pose_translator``` to separate the joints positions and send them to the controllers.

Then, using ```rqt_bag```, we could monitor these topics and save the trajectories for each joint.

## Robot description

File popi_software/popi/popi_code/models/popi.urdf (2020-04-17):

<robot name="popi">
    <link name="world" />
    <link name="base">
        <inertial>
            <origin xyz="0.00000 0.00000 -0.03523"/>
            <mass value="22.93400"/>
            <inertia ixx="0.38573" iyy="0.90692" izz="1.22770" ixy="-0.00000" ixz="-0.00000" iyz="-0.00000"/>
        </inertial>
    </link>
    <link name="EpauleAVD">
        <inertial>
            <origin xyz="-0.00354 0.04355 0.00137"/>
            <mass value="6.77500"/>
            <inertia ixx="0.02893" iyy="0.01067" izz="0.02860" ixy="-0.00075" ixz="0.00018" iyz="-0.00006"/>
        </inertial>
    </link>
    <link name="HJambeAVD">
        <inertial>
            <origin xyz="-0.11331 0.01743 -0.00512"/>
            <mass value="4.89500"/>
            <inertia ixx="0.00899" iyy="0.05703" izz="0.06050" ixy="0.00647" ixz="-0.00215" iyz="0.00043"/>
        </inertial>
    </link>
    <link name="BJambeAVD">
        <inertial>
            <origin xyz="0.11762 0.01239 0.00000"/>
            <mass value="0.49003"/>
            <inertia ixx="0.00010" iyy="0.00678" izz="0.00680" ixy="0.00019" ixz="0.00000" iyz="-0.00000"/>
        </inertial>
    </link>
    <link name="EpauleAVG">
        <inertial>
            <origin xyz="0.00354 -0.04355 -0.00137"/>
            <mass value="6.77500"/>
            <inertia ixx="0.02893" iyy="0.01067" izz="0.02864" ixy="-0.00075" ixz="0.00018" iyz="-0.00006"/>
        </inertial>
    </link>
    <link name="HJambeAVG">
        <inertial>
            <origin xyz="-0.11389 0.00901 0.00555"/>
            <mass value="4.95500"/>
            <inertia ixx="0.01032" iyy="0.05596" izz="0.06056" ixy="0.01011" ixz="0.00226" iyz="-0.00025"/>
        </inertial>
    </link>
    <link name="BJambeAVG">
        <inertial>
            <origin xyz="0.11762 0.01239 -0.00000"/>
            <mass value="0.49003"/>
            <inertia ixx="0.00010" iyy="0.00678" izz="0.00680" ixy="0.00019" ixz="0.00000" iyz="-0.00000"/>
        </inertial>
    </link>
    <link name="EpauleARD">
        <inertial>
            <origin xyz="-0.00354 0.04355 -0.00137"/>
            <mass value="6.77500"/>
            <inertia ixx="0.02893" iyy="0.01067" izz="0.02864" ixy="-0.00075" ixz="-0.00002" iyz="0.00006"/>
        </inertial>
    </link>
    <link name="HJambeARD">
        <inertial>
            <origin xyz="-0.11331 0.01743 -0.00512"/>
            <mass value="4.89500"/>
            <inertia ixx="0.00899" iyy="0.05703" izz="0.06050" ixy="0.00647" ixz="-0.00215" iyz="0.00043"/>
        </inertial>
    </link>
    <link name="BJambeARD">
        <inertial>
            <origin xyz="0.11762 0.01239 0.00000"/>
            <mass value="0.49003"/>
            <inertia ixx="0.00010" iyy="0.00678" izz="0.00680" ixy="0.00019" ixz="0.00000" iyz="-0.00000"/>
        </inertial>
    </link>
    <link name="EpauleARG">
        <inertial>
            <origin xyz="0.00354 -0.04355 0.00137"/>
            <mass value="6.77500"/>
            <inertia ixx="0.02893" iyy="0.01067" izz="0.02864" ixy="-0.00075" ixz="-0.00018" iyz="0.00006"/>
        </inertial>
    </link>
    <link name="HJambeARG">
        <inertial>
            <origin xyz="-0.11389 0.00901 0.00555"/>
            <mass value="4.95500"/>
            <inertia ixx="0.01032" iyy="0.05596" izz="0.06056" ixy="0.01011" ixz="0.00226" iyz="-0.00025"/>
        </inertial>
    </link>
    <link name="BJambeARG">
        <inertial>
            <origin xyz="0.11762 0.01239 -0.00000"/>
            <mass value="0.49003"/>
            <inertia ixx="0.00010" iyy="0.00678" izz="0.00680" ixy="0.00019" ixz="0.00000" iyz="-0.00000"/>
        </inertial>
    </link>
    <joint name="fbj" type="floating">
        <parent link="world"/>
        <child link="base"/>
    </joint>
    <joint name="rf_haa_joint" type="revolute">
        <origin xyz="0.33050 -0.17500 -0.05100" rpy="3.141592653589793 -1.570796282091413 3.141592653589793"/>
        <parent link="base"/>
        <child link="EpauleAVD"/>
        <limit effort="30" velocity="1.0"/>
        <axis xyz="0 0 1"/>
    </joint>
    <joint name="rf_hfe_joint" type="revolute">
        <origin xyz="0.00000 -0.10770 0.00000" rpy="-2.3561944901923457 1.5707962635746238 2.3561944901923457"/>
        <parent link="EpauleAVD"/>
        <child link="HJambeAVD"/>
        <limit effort="30" velocity="1.0"/>
        <axis xyz="0 0 1"/>
    </joint>
    <joint name="rf_kfe_joint" type="revolute">
        <origin xyz="-0.35192 -0.04151 -0.00000" rpy="3.1415925661670134 -0.0 0.0"/>
        <parent link="HJambeAVD"/>
        <child link="BJambeAVD"/>
        <limit effort="30" velocity="1.0"/>
        <axis xyz="0 0 1"/>
    </joint>
    <joint name="lf_haa_joint" type="revolute">
        <origin xyz="0.33050 0.17500 -0.05100" rpy="3.141592653589793 1.570796282091413 3.141592653589793"/>
        <parent link="base"/>
        <child link="EpauleAVG"/>
        <limit effort="30" velocity="1.0"/>
        <axis xyz="0 0 1"/>
    </joint>
    <joint name="lf_hfe_joint" type="revolute">
        <origin xyz="0.00000 0.10770 0.00000" rpy="-2.3561944901923457 -1.5707962635746238 -2.3561944901923457"/>
        <parent link="EpauleAVG"/>
        <child link="HJambeAVG"/>
        <limit effort="30" velocity="1.0"/>
        <axis xyz="0 0 1"/>
    </joint>
    <joint name="lf_kfe_joint" type="revolute">
        <origin xyz="-0.35192 -0.04151 -0.00000" rpy="3.1415925661670134 -0.0 0.0"/>
        <parent link="HJambeAVG"/>
        <child link="BJambeAVG"/>
        <limit effort="30" velocity="1.0"/>
        <axis xyz="0 0 1"/>
    </joint>
    <joint name="rh_haa_joint" type="revolute">
        <origin xyz="-0.33050 -0.17500 -0.05100" rpy="3.141592653589793 -1.570796282091413 3.141592653589793"/>
        <parent link="base"/>
        <child link="EpauleARD"/>
        <limit effort="30" velocity="1.0"/>
        <axis xyz="0 0 1"/>
    </joint>
    <joint name="rh_hfe_joint" type="revolute">
        <origin xyz="0.00000 -0.10770 0.00000" rpy="-2.3561944901923457 1.5707962635746238 2.3561944901923457"/>
        <parent link="EpauleARD"/>
        <child link="HJambeARD"/>
        <limit effort="30" velocity="1.0"/>
        <axis xyz="0 0 1"/>
    </joint>
    <joint name="rh_kfe_joint" type="revolute">
        <origin xyz="-0.35192 -0.04151 -0.00000" rpy="3.1415925661670134 -0.0 0.0"/>
        <parent link="HJambeARD"/>
        <child link="BJambeARD"/>
        <limit effort="30" velocity="1.0"/>
        <axis xyz="0 0 1"/>
    </joint>
    <joint name="lh_haa_joint" type="revolute">
        <origin xyz="-0.33050 0.17500 -0.05100" rpy="3.141592653589793 1.570796282091413 3.141592653589793"/>
        <parent link="base"/>
        <child link="EpauleARG"/>
        <limit effort="30" velocity="1.0"/>
        <axis xyz="0 0 1"/>
    </joint>
    <joint name="lh_hfe_joint" type="revolute">
        <origin xyz="0.00000 0.10770 0.00000" rpy="-2.3561944901923457 -1.5707962635746238 -2.3561944901923457"/>
        <parent link="EpauleARG"/>
        <child link="HJambeARG"/>
        <limit effort="30" velocity="1.0"/>
        <axis xyz="0 0 1"/>
    </joint>
    <joint name="lh_kfe_joint" type="revolute">
        <origin xyz="-0.35192 -0.04151 -0.00000" rpy="3.1415925661670134 -0.0 0.0"/>
        <parent link="HJambeARG"/>
        <child link="BJambeARG"/>
        <limit effort="30" velocity="1.0"/>
        <axis xyz="0 0 1"/>
    </joint>
</robot>

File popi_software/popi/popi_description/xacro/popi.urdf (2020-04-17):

<?xml version="1.0" encoding="utf-8"?>
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
<robot name="popi">

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

	<link name="Base_flottante">
        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
    </link>

    <joint name="base_flottante" type="fixed">
        <origin rpy="0 0 0" xyz="0 0 0"/>
        <parent link="Base_flottante"/>
        <child link="Bati"/>
    </joint>

  	<link name="Bati">
	    <inertial>
		    <origin xyz="0 0 -0.03523" rpy="0 0 0" />
		    <mass value="22.934" />
		    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
	    </inertial>
	    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
  	</link>
  	
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

  	<link name="EpauleAVD">
	    <inertial>
	      	<origin xyz="-0.00137 0.04355 -0.00354" rpy="0 0 0" />
	     	<mass value="6.775" />
	      	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
	    </inertial>
    	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
  	</link>
  	
  	<link name="HJambeAVD">
    	<inertial>
     		<origin xyz="-0.11331 0.00512 0.01743" rpy="0 0 0" />
      		<mass value="4.895" />
      		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
    	</inertial>
    	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
  	</link>
  	
  	<link name="BJambeAVD">
    	<inertial>
      		<origin xyz="0.11761 0 -0.012387" rpy="0 0 0" />
      		<mass value="0.49" />
      		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
    	</inertial>
    	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
  	</link>
  	
  	<link name="PiedAVD">
    	<inertial>
      		<origin xyz="0.0005 1.1348E-09 -1.2018E-09" rpy="0 0 0" />
      		<mass value="2.5E-05" />
      		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
    	</inertial>
    	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
  	</link>
    
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

    <link name="EpauleAVG">
    	<inertial>
      		<origin xyz="-0.00137 -0.04355 -0.00354" rpy="0 0 0" />
      		<mass value="6.775" />
      		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
    	</inertial>
    	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
  	</link>
	
	<link name="HJambeAVG">
	    <inertial>
	      	<origin xyz="-0.11389 -0.00555 0.00901" rpy="0 0 0" />
	      	<mass value="4.955" />
	      	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
	    </inertial>
	    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
	</link>
	
	<link name="BJambeAVG">
	    <inertial>
	      	<origin xyz="0.11761 0 -0.012387" rpy="0 0 0" />
	      	<mass value="0.49" />
	      	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
	    </inertial>
	    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
	</link>

	<link name="PiedAVG">
    	<inertial>
      		<origin xyz="0.0005 -3.5068E-06 -4.4931E-09" rpy="0 0 0" />
      		<mass value="2.5E-05" />
      		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
    	</inertial>
	    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
  	</link>

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	
	<link name="EpauleARD">
	    <inertial>
	      	<origin xyz="0.00137 0.04355 -0.00354" rpy="0 0 0" />
	      	<mass value="6.775" />
	     	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
	    </inertial>
	    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
	</link>

	<link name="HJambeARD">
	    <inertial>
	     	<origin xyz="-0.11331 0.00512 0.01743" rpy="0 0 0" /> 
	      	<mass value="4.895" />
	      	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
	    </inertial>
	    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
	</link>

  	<link name="BJambeARD">
	    <inertial>
	      	<origin xyz="0.11761 0 -0.012387" rpy="0 0 0" />
	      	<mass value="0.49" />
	      	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
	    </inertial>
	    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
  	</link>	

	<link name="PiedARD">
	    <inertial>
	      	<origin xyz="0.0005 -3.0378E-12 -8.2379E-14" rpy="0 0 0" />
	      	<mass value="2.5E-05" />
	    	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
	    </inertial>
	    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
	</link>

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
  	
  	<link name="EpauleARG">
	    <inertial>
	      	<origin xyz="0.00137 -0.04355 -0.00354" rpy="0 0 0" />
	      	<mass value="6.775" />
	      	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
	    </inertial>
    	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
  	</link>

	<link name="HJambeARG">
	    <inertial>
	      	<origin xyz="-0.11389 -0.00555 0.00901" rpy="0 0 0" />
	      	<mass value="4.955" />
	      	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
	    </inertial>
	    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
	</link>

	<link name="BJambeARG">
	    <inertial>
	      	<origin xyz="0.11761 0.0 -0.012387" rpy="0 0 0" />
	      	<mass value="0.49" />
	      	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
	    </inertial>
	    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
	</link>

	<link name="PiedARG">
	    <inertial>
	      	<origin xyz="0.0005 -3.5073E-06 5.5511E-14" rpy="0 0 0" />
	      	<mass value="2.5E-05" />
	      	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
	    </inertial>
	    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
	</link>

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

  	<joint name="aileAVD" type="revolute">
    	<origin xyz="0.3305 -0.175 -0.051" rpy="0 0 0" />
    	<parent link="Bati" />
    	<child link="EpauleAVD" />
    	<axis xyz="-1 0 0" />
    	<limit lower="-0.4" upper="0.4" effort="120" velocity="3.14159" />
	</joint>

	<joint name="epauleAVD" type="revolute">
	    <origin xyz="0 -0.1077 0" rpy="0 0 0" />
	    <parent link="EpauleAVD" />
	    <child link="HJambeAVD" />
	    <axis xyz="0 -1 0" />
	    <limit lower="0" upper="3.14159" effort="122" velocity="2.87" />
  	</joint>

  	<joint name="coudeAVD" type="revolute">
	    <origin xyz="-0.35192 0 -0.041509" rpy="0 0 0" />
	    <parent link="HJambeAVD" />
	    <child link="BJambeAVD" />
	    <axis xyz="0 1 0" />
	    <limit lower="0.2" upper="2.2" effort="1000" velocity="3.14159" />
  	</joint>

  	<joint name="piedAVD" type="fixed">
	    <origin xyz="0.29604 0 -0.015" rpy="0 0 0" />
	    <parent link="BJambeAVD" />
	    <child link="PiedAVD" />
	    <axis xyz="0 0 0" />
  	</joint>

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

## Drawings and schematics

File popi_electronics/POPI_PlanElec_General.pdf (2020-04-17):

## Epaule Epaule

# PwmAileAvD GND GND GND

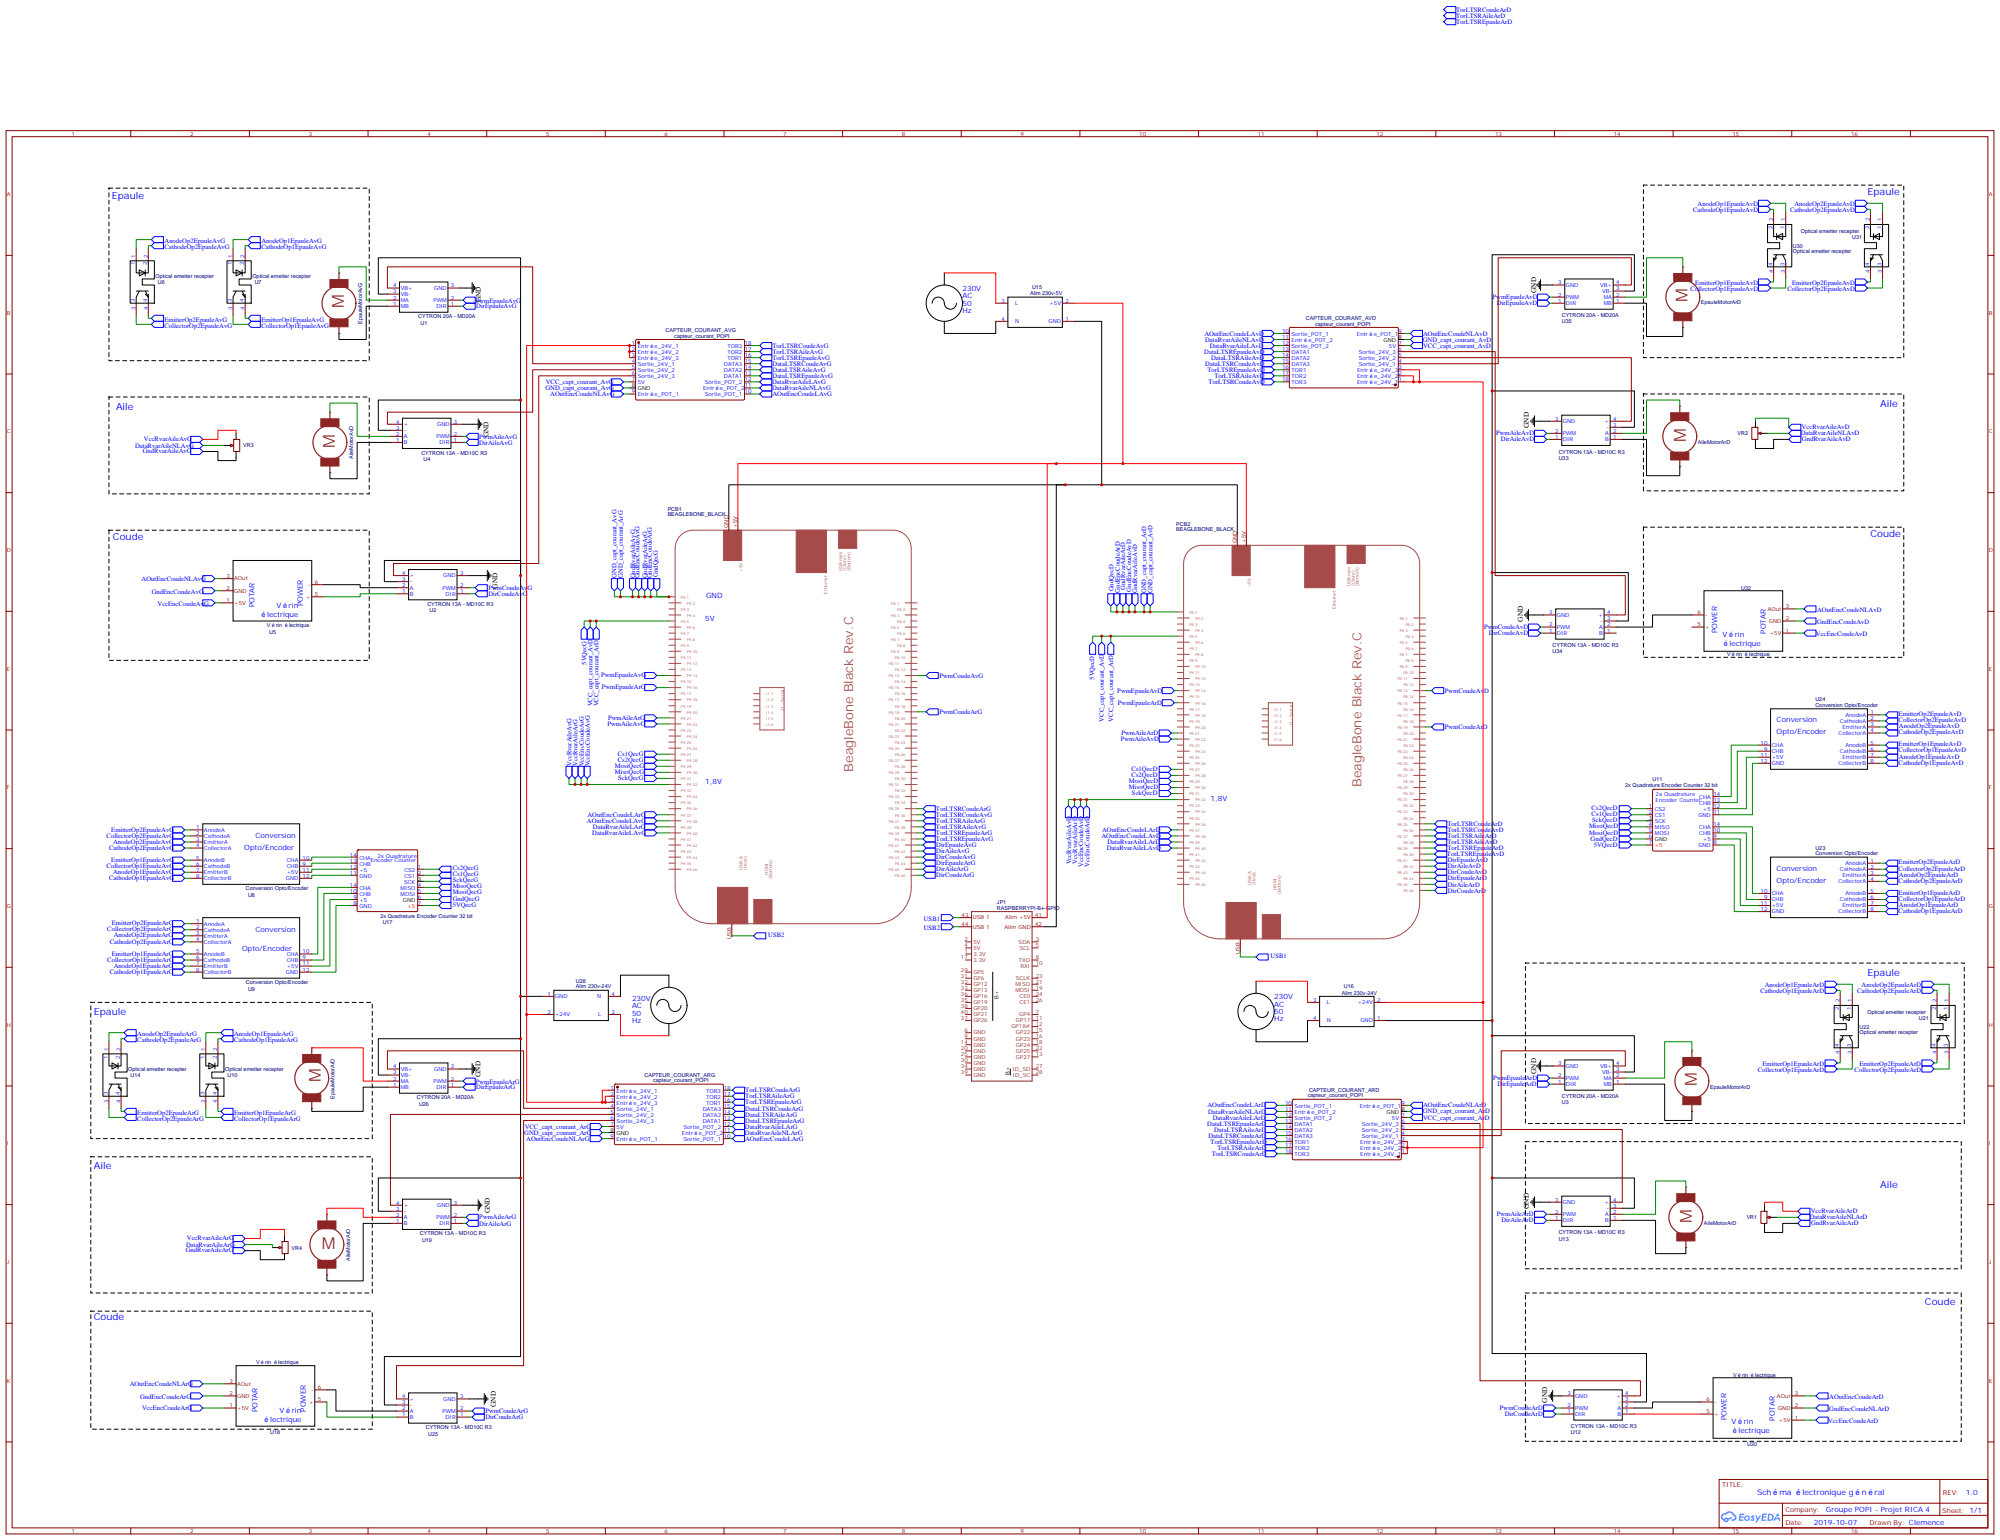
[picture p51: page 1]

2x Quadrature Encoder Counter 32 bit

Company: Groupe POPI - Projet RICA 4

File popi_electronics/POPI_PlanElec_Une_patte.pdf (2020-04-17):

## Epaule

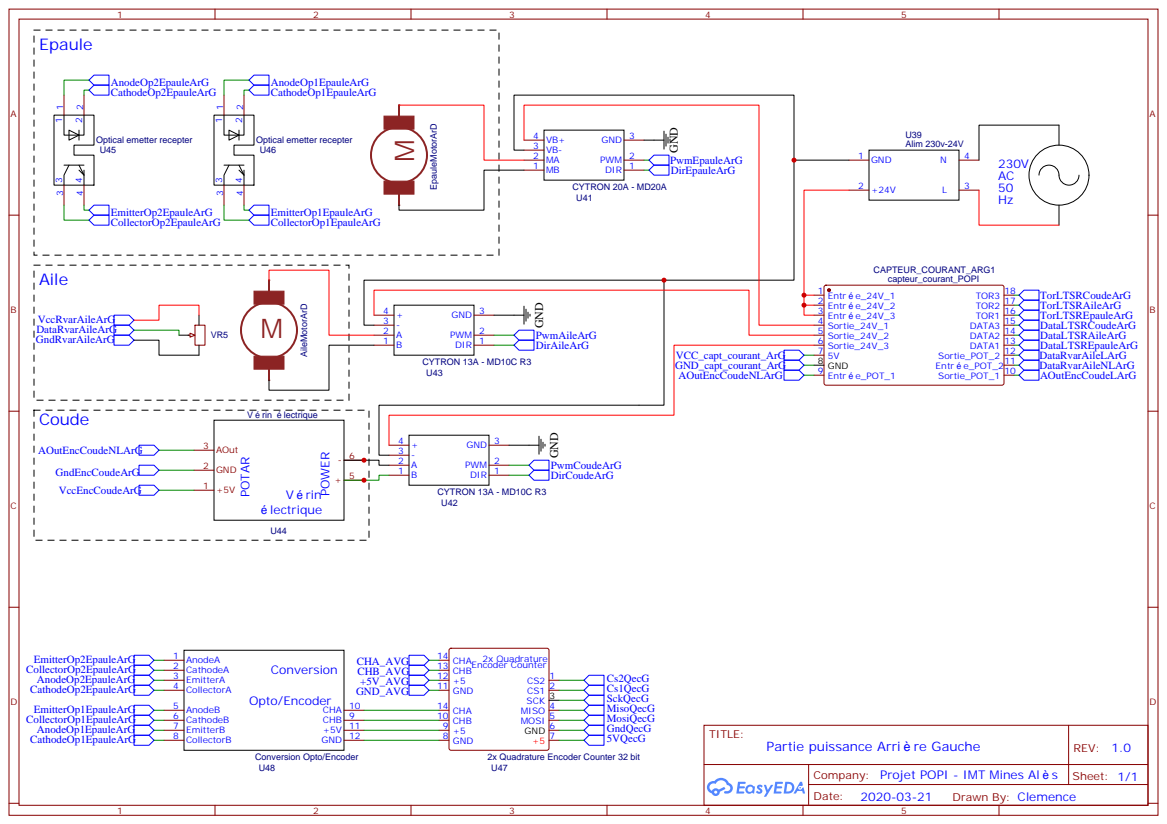
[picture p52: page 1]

2x Quadrature Encoder Counter 32 bit

Company: Projet POPI - IMT Mines Al s

# VccEncCoudeAvGGndRvarAileAvG GndEncCoudeAvG

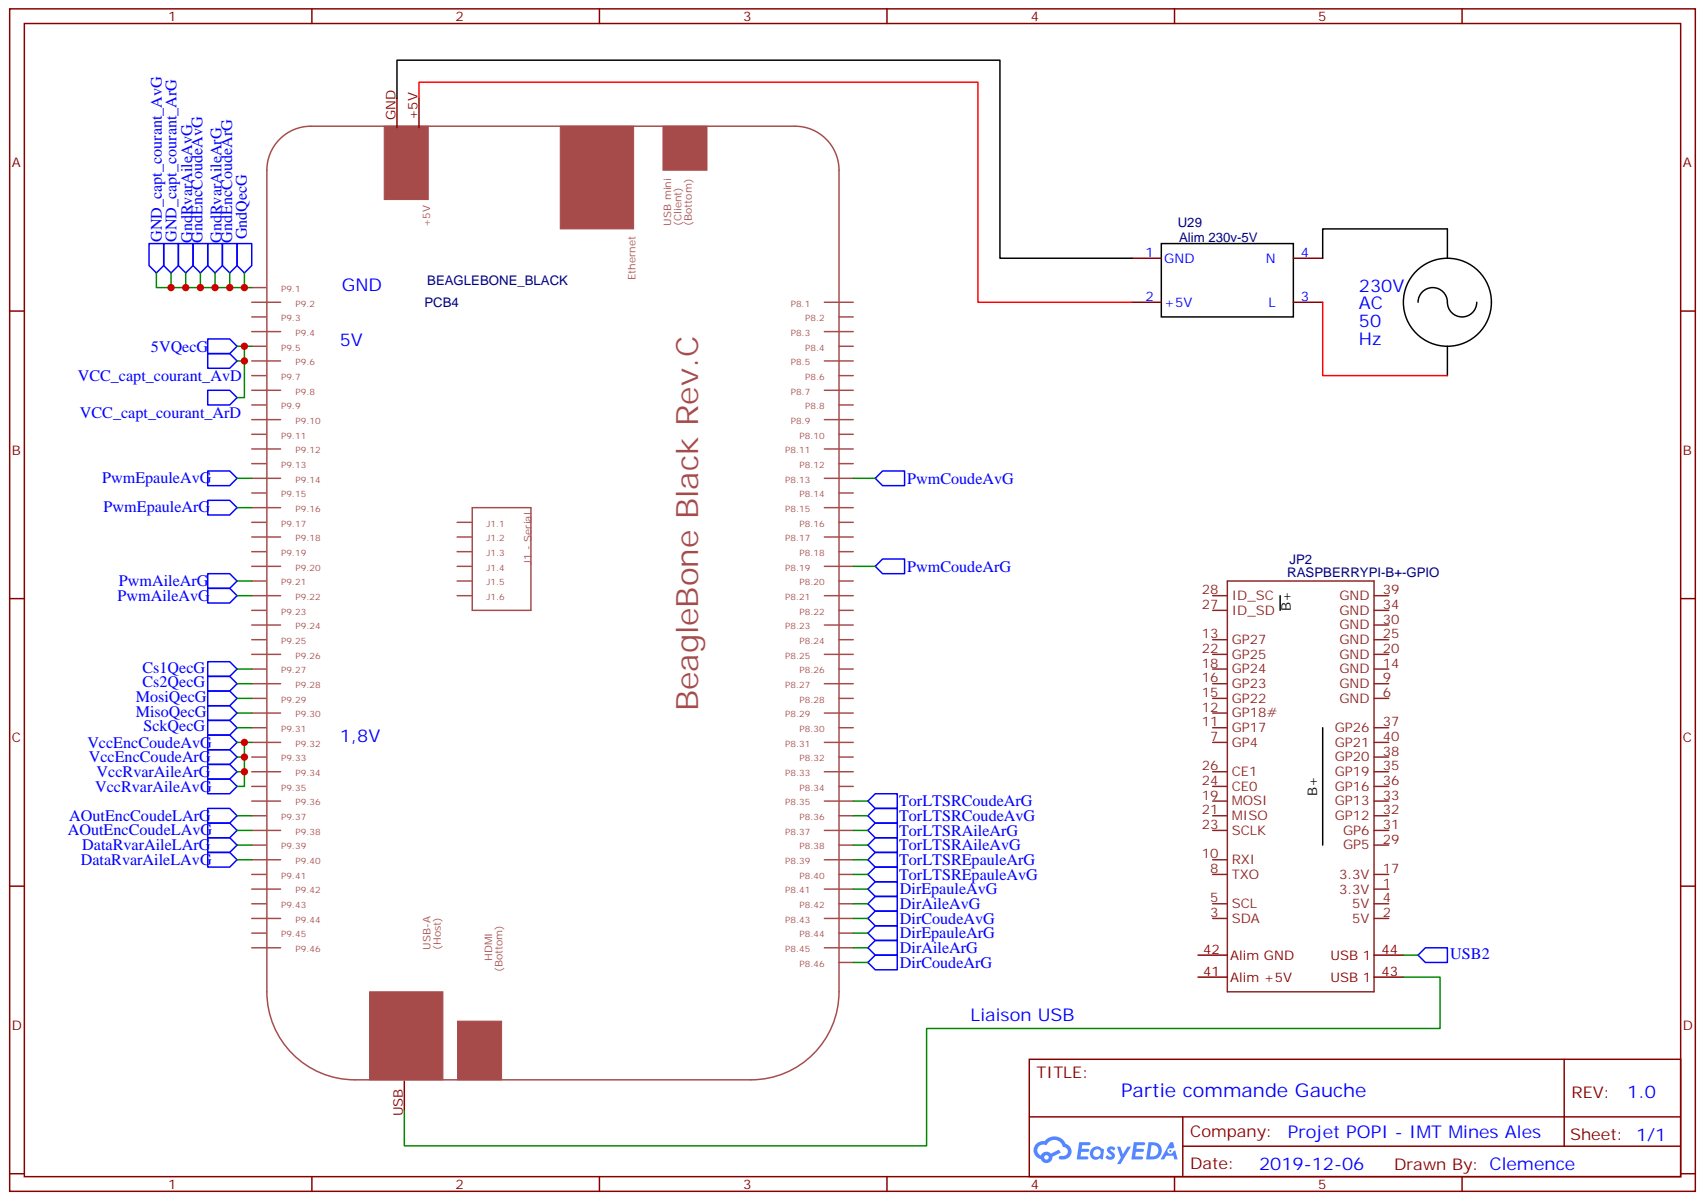
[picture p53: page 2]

Company: Projet POPI - IMT Mines Ales

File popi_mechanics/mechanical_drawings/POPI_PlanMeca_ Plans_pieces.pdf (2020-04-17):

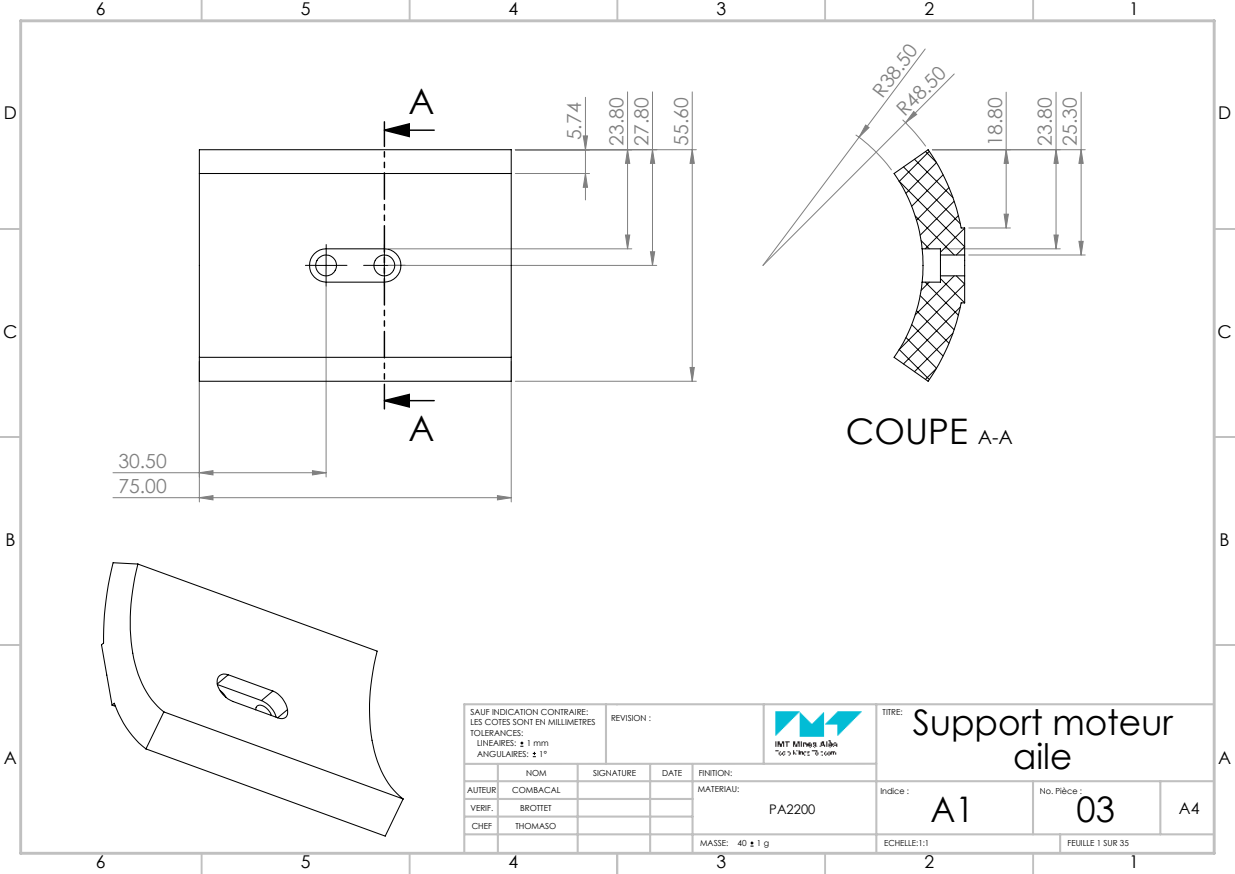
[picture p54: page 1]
COUPE A-A; aile AUTEUR

SAUF INDICATION CONTRAIRE: LES COTES SONT EN MILLIMETRES TOLERANCES: LINEAIRES: 1 mm ANGULAIRES: 1° | REVISION : | | Support moteur TITRE:

NOM | SIGNATURE | DATE | FINITION:
COMBACAL | | | MATERIAU: PA2200 | Indice : A1 | No. Pièce : 03 | A4

VERIF. | BROTTET
CHEF | THOMASO

MASSE: 40 1 g | ECHELLE:1:1 | FEUILLE 1 SUR 35

COUPE A-A
Plaque verticale intérieure AUTEUR

SAUF INDICATION CONTRAIRE: LES COTES SONT EN MILLIMETRES TOLERANCES: LINEAIRES: 1 mm ANGULAIRES: 1° | REVISION : Ajout de perçages pour les accroches ombilic sur le haut de la plaque. | | TITRE:

NOM | SIGNATURE | DATE | FINITION:
COMBACAL | | | MATERIAU: Aluminium | Indice : B1 | No. Pièce : 04 | A4

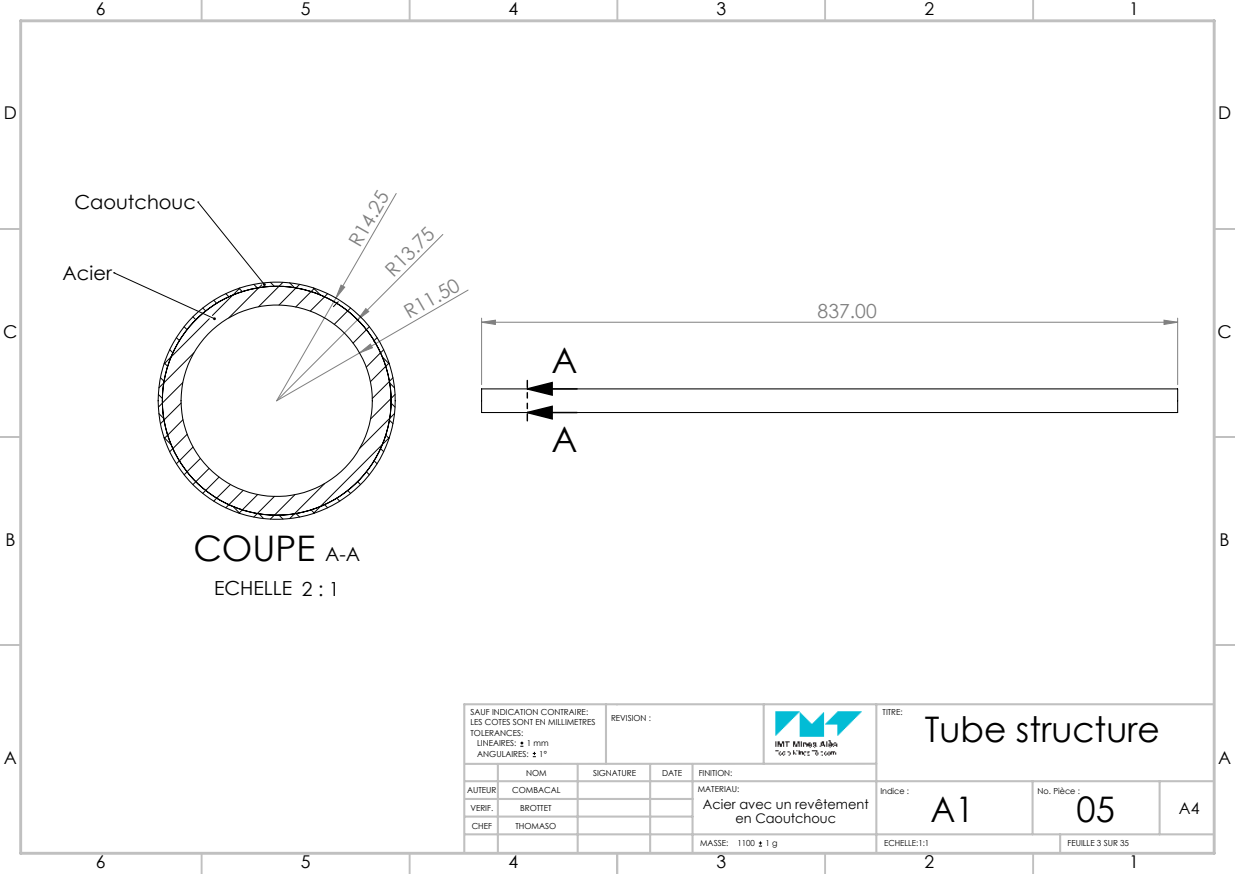
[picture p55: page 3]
COUPE A-A; ECHELLE 2 : 1; ECHELLE:1:1; FEUILLE 3 SUR 35

SAUF INDICATION CONTRAIRE: LES COTES SONT EN MILLIMETRES TOLERANCES: LINEAIRES: 1 mm ANGULAIRES: 1° | REVISION : | | TITRE: Tube structure

NOM | SIGNATURE | DATE | FINITION:

AUTEUR | COMBACAL | | | MATERIAU: Acier avec un revêtement | Indice : A1 | No. Pièce : 05 | A4 en Caoutchouc

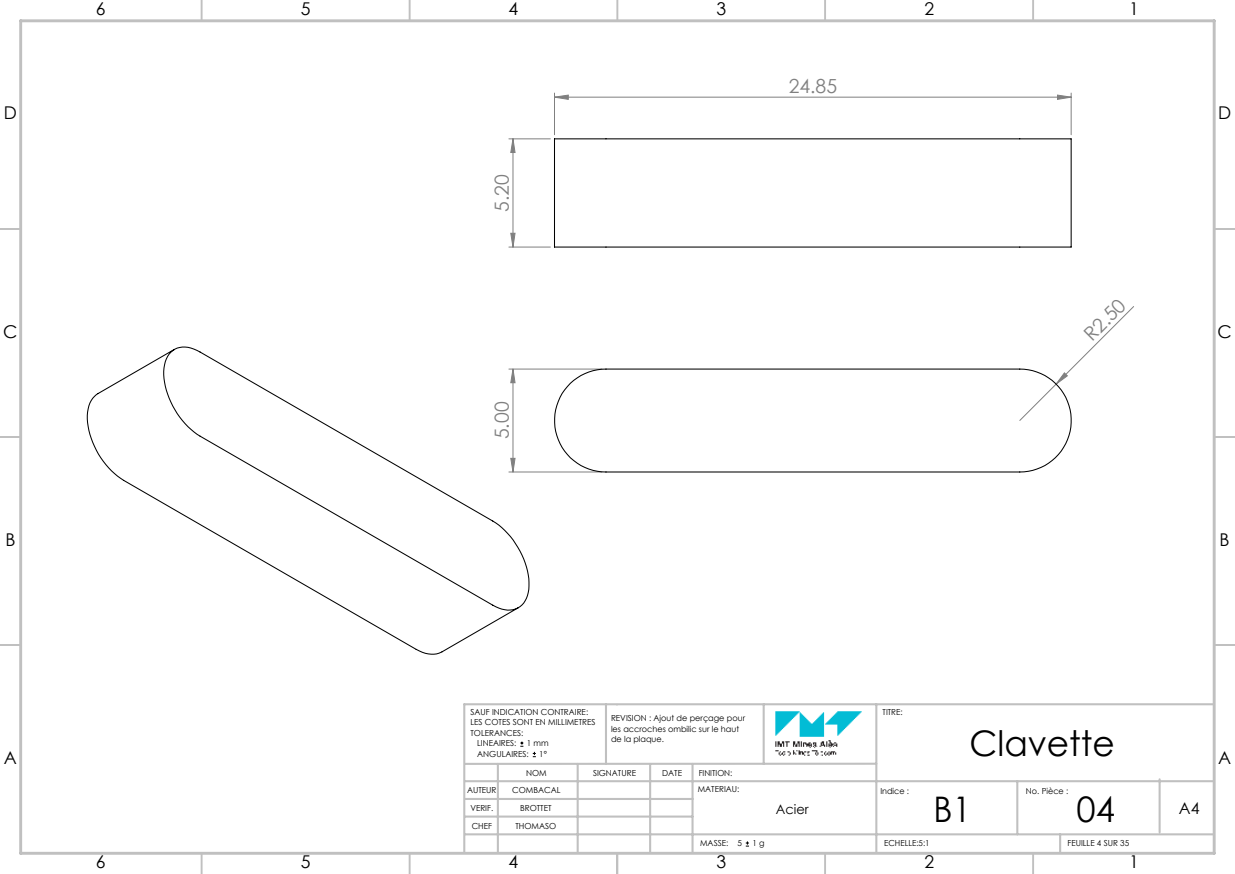
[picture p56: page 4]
ECHELLE:5:1; FEUILLE 4 SUR 35

SAUF INDICATION CONTRAIRE: LES COTES SONT EN MILLIMETRES TOLERANCES: LINEAIRES: 1 mm ANGULAIRES: 1° | REVISION : Ajout de perçage pour les accroches ombilic sur le haut de la plaque. | | TITRE: Clavette

NOM | SIGNATURE | DATE | FINITION:

AUTEUR | COMBACAL | | | MATERIAU: Acier | Indice : B1 | No. Pièce : 04 | A4

SAUF INDICATION CONTRAIRE: LES COTES SONT EN MILLIMETRES TOLERANCES: LINEAIRES: 1 mm ANGULAIRES: 1° | REVISION : Ajout de percages sur la face latérale afin de venir serrer les axes avec des pointeaux. | | TITRE: Porte réducteur

NOM | SIGNATURE | DATE | FINITION:

AUTEUR | | | | MATERIAU: | B1 Indice : | No. Pièce : 08 COMBACAL

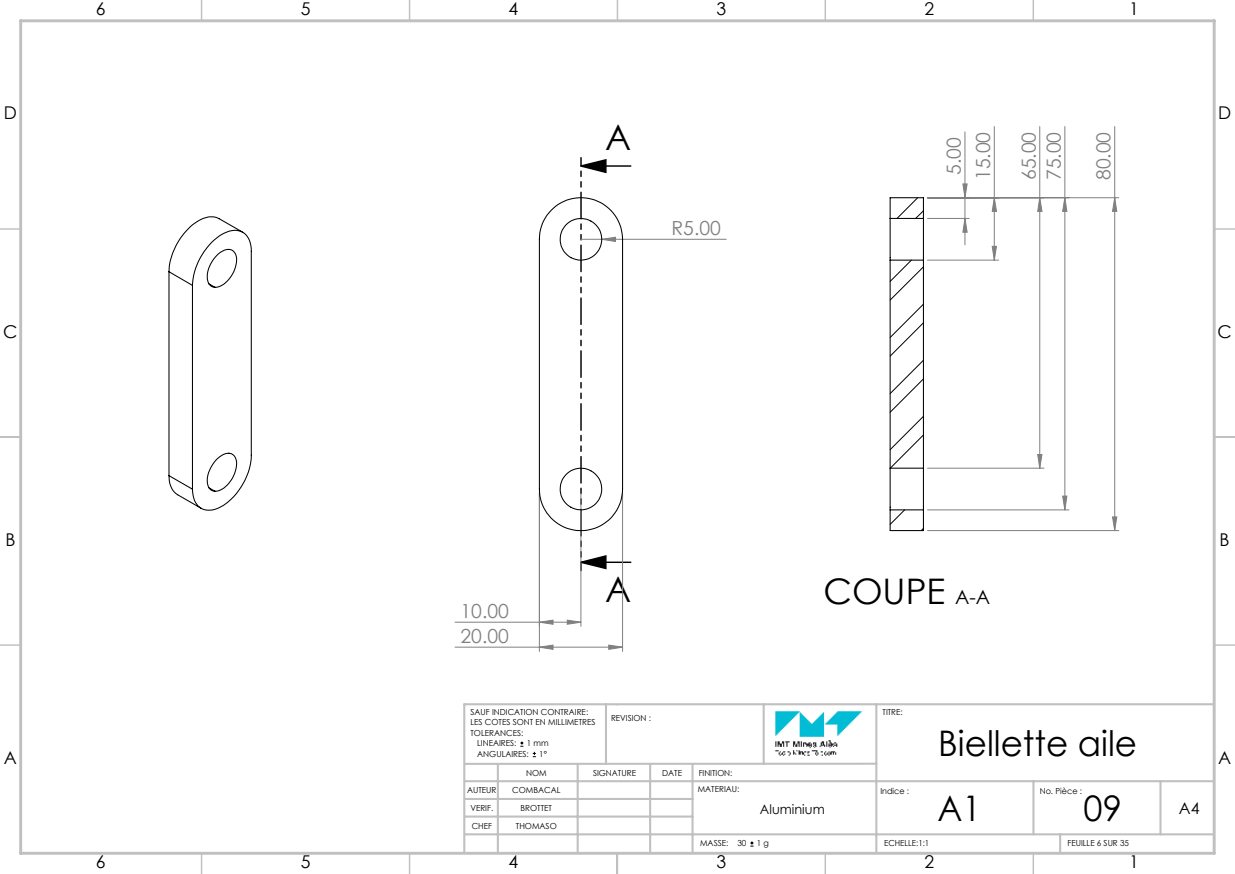
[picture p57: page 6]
COUPE A-A; ECHELLE:1:1; FEUILLE 6 SUR 35

SAUF INDICATION CONTRAIRE: LES COTES SONT EN MILLIMETRES TOLERANCES: LINEAIRES: 1 mm ANGULAIRES: 1° | REVISION : | | TITRE: Biellette aile

NOM | SIGNATURE | DATE | FINITION:

AUTEUR | | | | MATERIAU: | Indice : A1 | No. Pièce : 09 COMBACAL

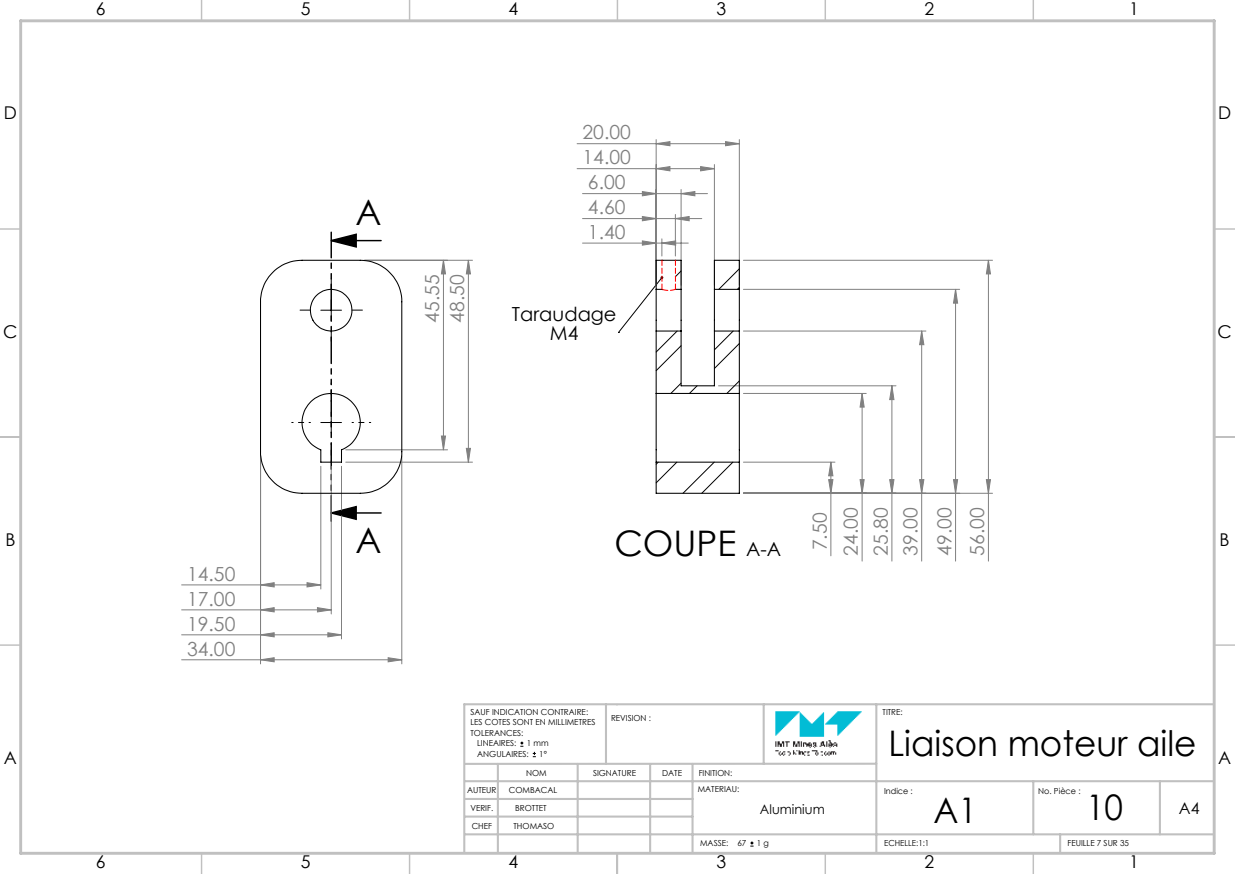
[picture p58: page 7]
COUPE A-A; ECHELLE:1:1; FEUILLE 7 SUR 35

SAUF INDICATION CONTRAIRE: LES COTES SONT EN MILLIMETRES TOLERANCES: LINEAIRES: 1 mm ANGULAIRES: 1° | REVISION : | | TITRE: Liaison moteur aile

NOM | SIGNATURE | DATE | FINITION:

AUTEUR | | | | MATERIAU: | Indice : A1 COMBACAL | No. Pièce : 10

SAUF INDICATION CONTRAIRE: LES COTES SONT EN MILLIMETRES TOLERANCES: LINEAIRES: 1 mm ANGULAIRES: 1° | REVISION : | | Plaque verticale extérieure AUTEUR TITRE:

NOM | SIGNATURE | DATE | FINITION:
COMBCAL | | | MATERIAU: | Indice : A1 | No. Pièce : 11

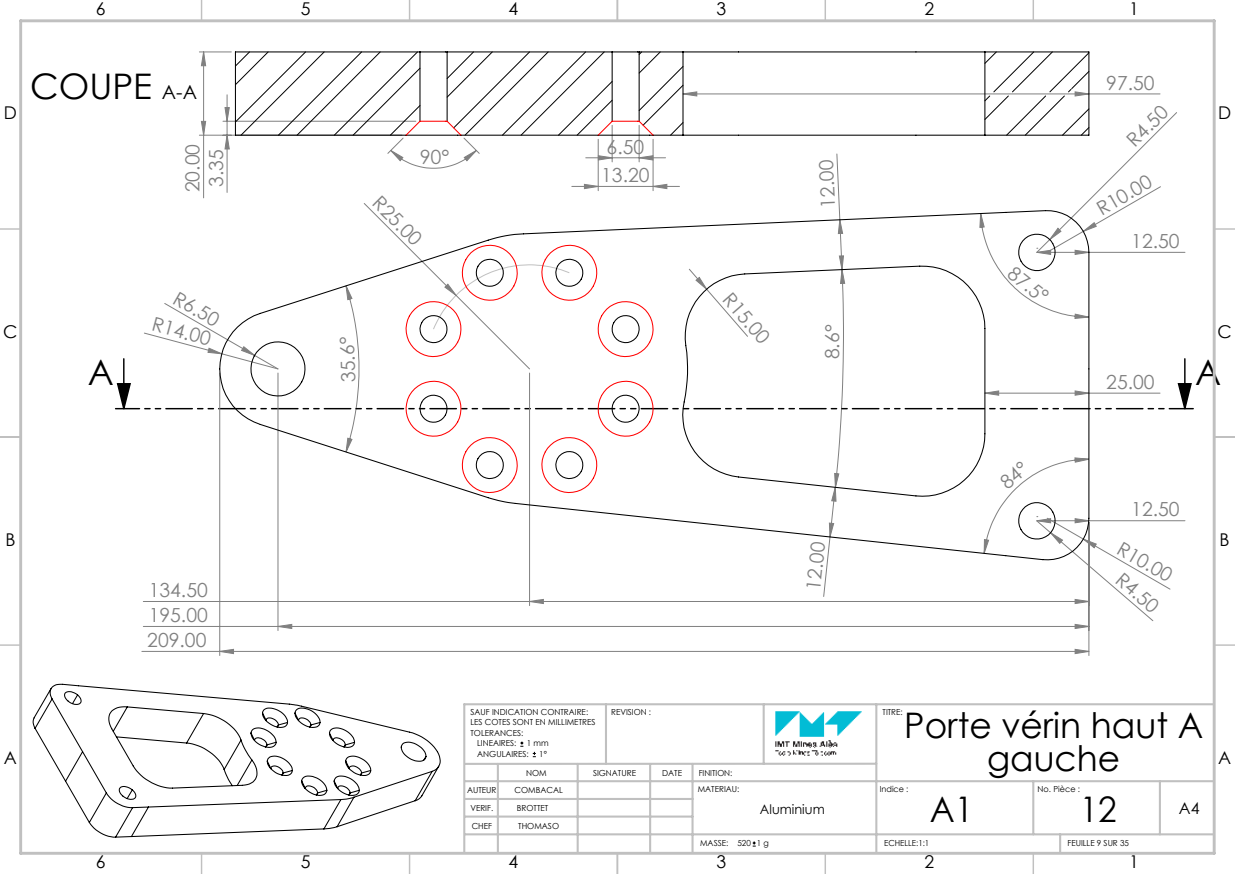
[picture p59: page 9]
COUPE; ECHELLE:1:1; FEUILLE 9 SUR 35; gauche AUTEUR

SAUF INDICATION CONTRAIRE: LES COTES SONT EN MILLIMETRES TOLERANCES: LINEAIRES: 1 mm ANGULAIRES: 1° | REVISION : | | Porte vérin haut A TITRE:

NOM | SIGNATURE | DATE | FINITION:
COMBACAL | | | MATERIAU: | Indice : A1 | No. Pièce : 12

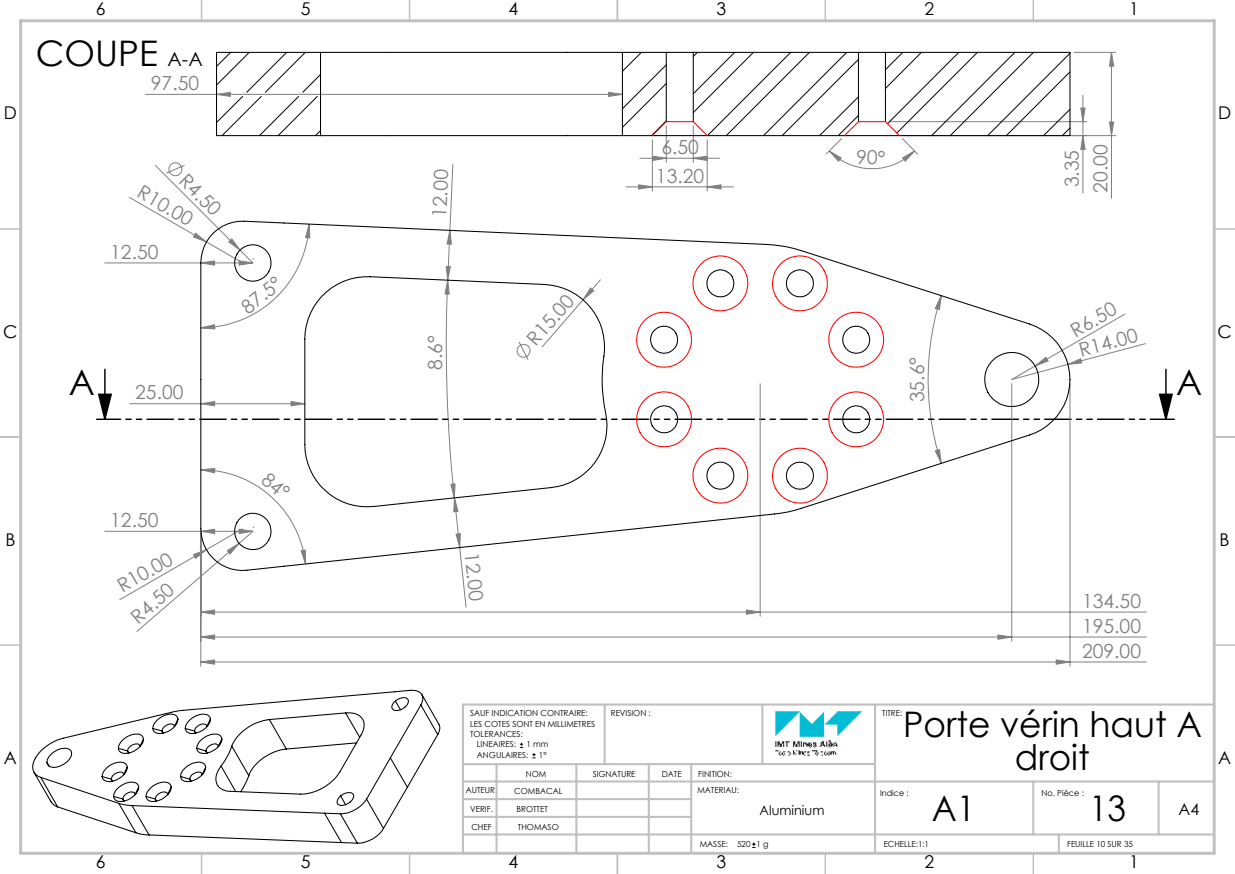
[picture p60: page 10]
COUPE A-A; ECHELLE:1:1; FEUILLE 10 SUR 35

SAUF INDICATION CONTRAIRE: LES COTES SONT EN MILLIMETRES TOLERANCES: LINEAIRES: 1 mm ANGULAIRES: 1° | REVISION : | | Porte vérin haut A TITRE: droit

NOM | SIGNATURE | DATE | FINITION:

COMBACAL | | | MATERIAU: | A1 MASSE: Indice : | No. Pièce : 13
AUTEUR

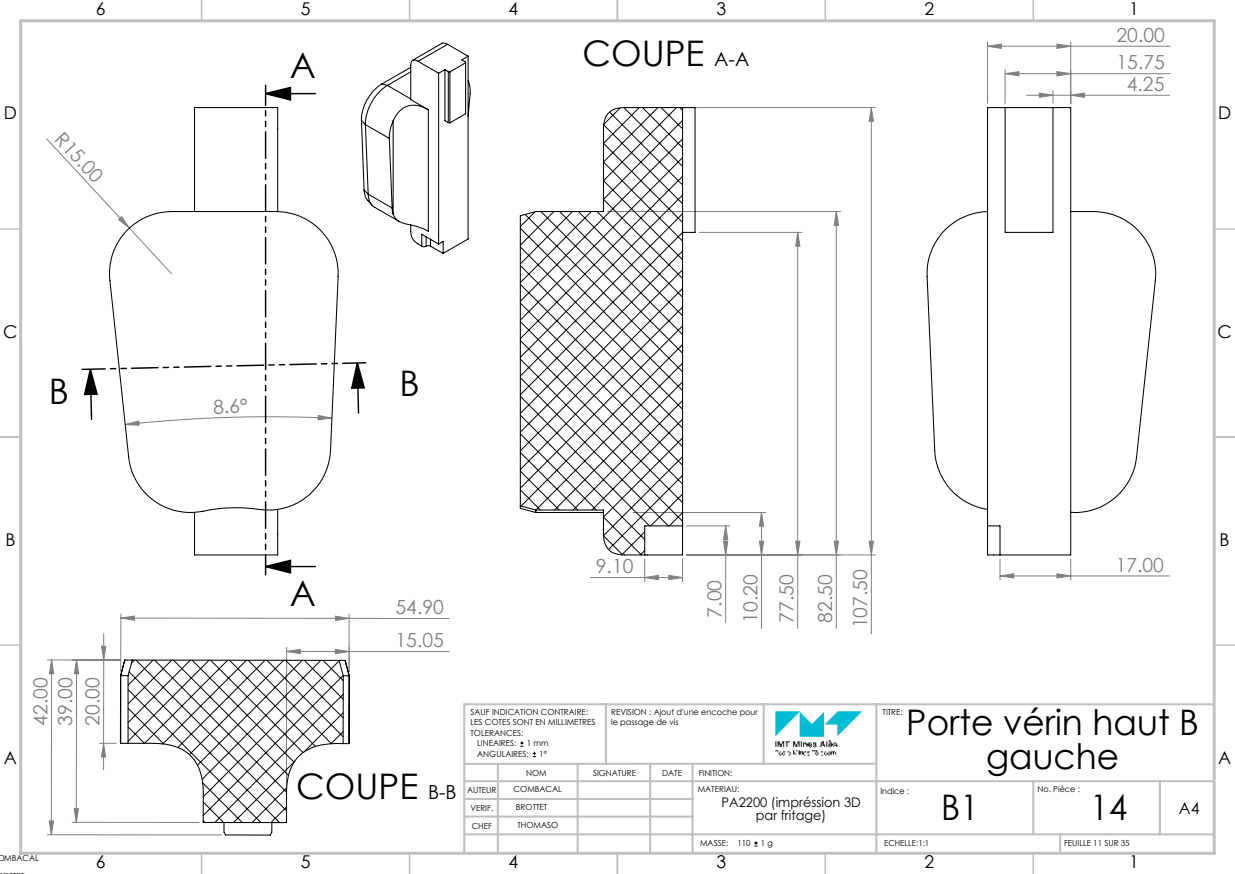
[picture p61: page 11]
COUPE A-A; COUPE B-B; VERIF.; ECHELLE:1:1; FEUILLE 11 SUR 35; gauche AUTEUR

SAUF INDICATION CONTRAIRE: LES COTES SONT EN MILLIMETRES TOLERANCES: LINEAIRES: 1 mm ANGULAIRES: 1° | REVISION : Ajout d'une encoche pour le passage de vis | | Porte vérin haut B TITRE:

NOM | SIGNATURE | DATE | FINITION:
COMBACAL | | | MATERIAU: PA2200 (impréssion 3D par fritage) | Indice : B1 | No. Pièce : 14 | A4

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

NOM | SIGNATURE | DATE | FINITION:
COMBACAL | | | MATERIAU: PA2200 (impréssion 3D par fritage) | Indice : B1 | No. Pièce : 15 | A4
THOMASO

ECHELLE:1:1 | FEUILLE 12 SUR 35

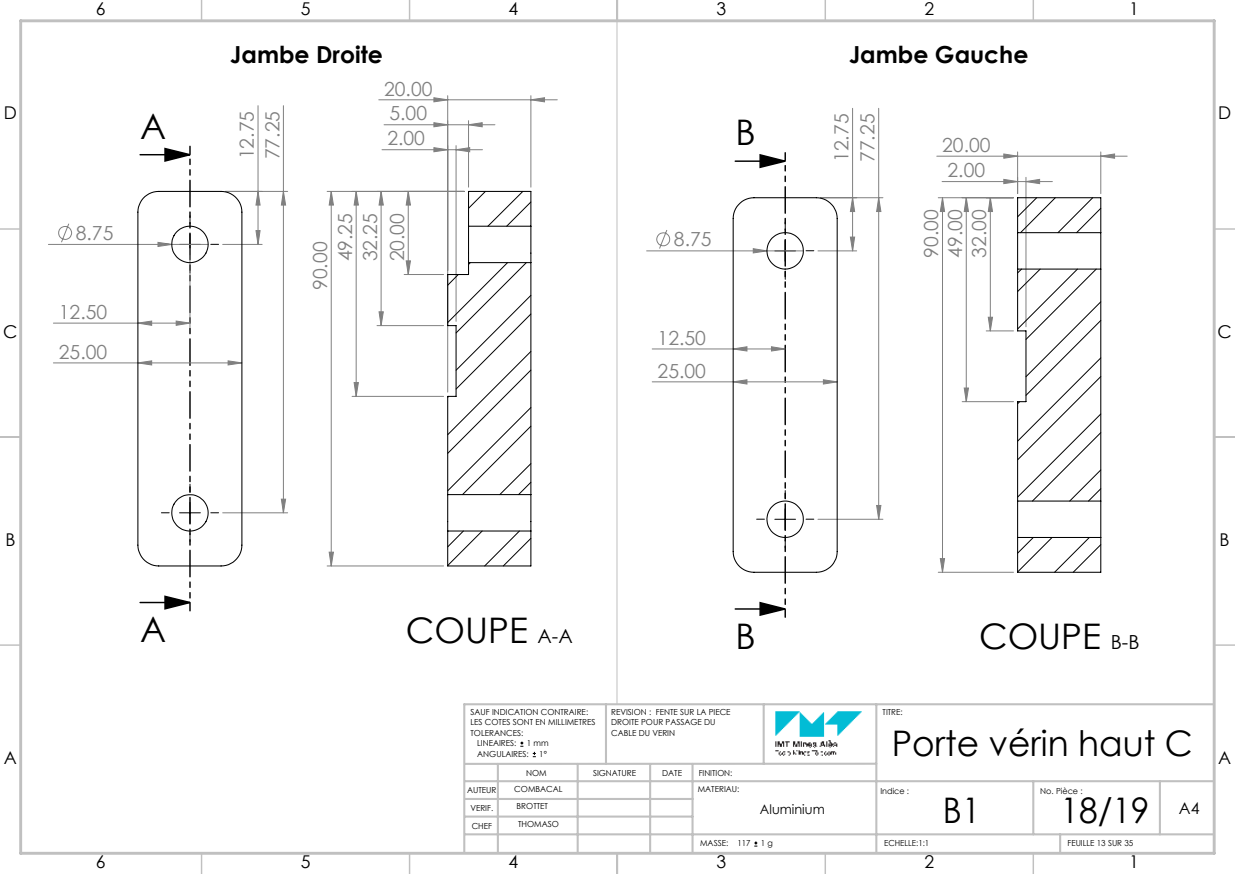
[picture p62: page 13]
COUPE A-A; COUPE B-B; Jambe Droite; Jambe Gauche; ECHELLE:1:1; FEUILLE 13 SUR 35

20.00
2.00

SAUF INDICATION CONTRAIRE: LES COTES SONT EN MILLIMETRES TOLERANCES: LINEAIRES: 1 mm ANGULAIRES: 1° | REVISION : FENTE SUR LA PIECE DROITE POUR PASSAGE DU CABLE DU VERIN | | TITRE: Porte vérin haut C

NOM | SIGNATURE | DATE | FINITION:

AUTEUR | COMBACAL | | | MATERIAU: | Indice : B1 | No. Pièce : 18/19
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

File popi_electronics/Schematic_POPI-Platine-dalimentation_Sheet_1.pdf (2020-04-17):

Depuis PC COM | L N | Depuis reseau domestique






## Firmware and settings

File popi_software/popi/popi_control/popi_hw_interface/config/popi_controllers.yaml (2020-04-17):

# popi_control Settings -----------------------
# Settings for ros_control control loop
generic_hw_control_loop:
  loop_hz: 20
  cycle_time_error_threshold: 0.05

# Settings for ros_control hardware interface
hardware_interface:
   joints:
      - joint1
      - joint2
   sim_control_mode: 0 # 0: position, 1: velocity

# Publish all joint states ----------------------------------
# Creates the /joint_states topic necessary in ROS
joint_state_controller:
   type: joint_state_controller/JointStateController
   publish_rate: 50

# Joint Trajectory Controller -------------------------------
# For detailed explanations of parameter see http://wiki.ros.org/joint_trajectory_controller
position_trajectory_controller:
   type: position_controllers/JointTrajectoryController
   # These joints can likely just be copied from the hardware_interface list above
   joints:
      - joint1
      - joint2
   constraints:
      goal_time: 5.0
      #stopped_position_tolerance: 0.4 # Defaults to 0.01
      joint1:
          trajectory: 0.60
          goal:       0.15
      joint2:
          trajectory: 0.60
          goal:       0.15
   # gains:
   #     joint1: {p: 2.0,  i: 0.0, d: 0.01, i_clamp: 1}
   #     joint2: {p: 2.0,  i: 0.0, d: 0.01, i_clamp: 1}

    # state_publish_rate:  50 # Defaults to 50
    # action_monitor_rate: 20 # Defaults to 20
    #hold_trajectory_duration: 0 # Defaults to 0.5

# Individual Position Controllers ---------------------------------------
# Allows to send individual ROS msg of Float64 to each joint separately
joint1_position_controller:
   type: position_controllers/JointPositionController
   joint: joint1
   pid: {p: 100.0, i: 0.01, d: 10.0}
joint2_position_controller:
   type: position_controllers/JointPositionController
   joint: joint2
   pid: {p: 100.0, i: 0.01, d: 10.0}

# Group Position Controllers ---------------------------------------
# Allows to send single ROS msg of Float64MultiArray to all joints
joint_position_controller:
   type: position_controllers/JointGroupPositionController
   joints:
     - joint1
     - joint2


joint1_eff_position_controller:
   type: effort_controllers/JointPositionController
   joint: joint1
   pid: {p: 100.0, i: 0.0, d: 1.0}
joint2_eff_position_controller:
   type: effort_controllers/JointPositionController
   joint: joint2
   pid: {p: 100.0, i: 0.0, d: 1.0}

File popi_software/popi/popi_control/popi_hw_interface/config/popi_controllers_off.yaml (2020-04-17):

# popi_control Settings -----------------------
# Settings for ros_control control loop
generic_hw_control_loop:
  loop_hz: 100
  cycle_time_error_threshold: 0.2

# Settings for ros_control hardware interface
hardware_interface:
   joints:
      - aileAVD
      - epauleAVD
      - coudeAVD

      - aileAVG
      - epauleAVG
      - coudeAVG

      - aileARD
      - epauleARD
      - coudeARD

      - aileARG
      - epauleARG
      - coudeARG
   sim_control_mode: 0 # 0: position, 1: velocity

# Publish all joint states ----------------------------------
# Creates the /joint_states topic necessary in ROS
joint_state_controller:
   type: joint_state_controller/JointStateController
   publish_rate: 100

aileAVD_eff_position_controller:
   type: effort_controllers/JointPositionController
   joint: aileAVD
   pid: {p: 0.0, i: 0.0, d: 0.0}
epauleAVD_eff_position_controller:
   type: effort_controllers/JointPositionController
   joint: epauleAVD
   pid: {p: 0.0, i: 0.0, d: 0.0}
coudeAVD_eff_position_controller:
   type: effort_controllers/JointPositionController
   joint: coudeAVD
   pid: {p: 0.0, i: 0.0, d: 0.0}

aileAVG_eff_position_controller:
   type: effort_controllers/JointPositionController
   joint: aileAVG
   pid: {p: 0.0, i: 0.0, d: 0.0}
epauleAVG_eff_position_controller:
   type: effort_controllers/JointPositionController
   joint: epauleAVG
   pid: {p: 0.0, i: 0.0, d: 0.0}
coudeAVG_eff_position_controller:
   type: effort_controllers/JointPositionController
   joint: coudeAVG
   pid: {p: 0.0, i: 0.0, d: 0.0}

aileARD_eff_position_controller:
   type: effort_controllers/JointPositionController
   joint: aileARD
   pid: {p: 0.0, i: 0.0, d: 0.0}
epauleARD_eff_position_controller:
   type: effort_controllers/JointPositionController
   joint: epauleARD
   pid: {p: 0.0, i: 0.0, d: 0.0}
coudeARD_eff_position_controller:
   type: effort_controllers/JointPositionController
   joint: coudeARD
   pid: {p: 0.0, i: 0.0, d: 0.0}

aileARG_eff_position_controller:
   type: effort_controllers/JointPositionController
   joint: aileARG
   pid: {p: 0.0, i: 0.0, d: 0.0}
epauleARG_eff_position_controller:
   type: effort_controllers/JointPositionController
   joint: epauleARG
   pid: {p: 0.0, i: 0.0, d: 0.0}
coudeARG_eff_position_controller:
   type: effort_controllers/JointPositionController
   joint: coudeARG
   pid: {p: 0.0, i: 0.0, d: 0.0}
